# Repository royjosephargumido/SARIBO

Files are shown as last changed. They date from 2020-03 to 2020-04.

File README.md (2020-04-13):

# Overview
  
**SARIBO** or ***Systematic and Automated Regulation of Irrigation systems for Backyard farming Operations*** is an internet-of-things (IOT) Irrigation System designed for Backyard Farming created using ESP8266 NodeMCU 12E v3 (LoLin). SARIBO is a waray-waray (Waray) term for "to water" especially for plants.

SARIBO contains two modules:

1. **SARIBO Leaf Module (SARIBO Leaf).** The SARIBO Leaf Module which controls the connected sensors and is placed on the field.
2. **SARIBO Root Module (SARIBO Root).** The SARIBO Root Module is the main controller module which controls the watering process, activation of relays for the pump and valves, water level among others.

# Stable Version

See the official stable version @ **[Official Stable Release SARIBO version 1.2.7](https://github.com/rjargumido/SARIBO/releases/tag/v.1.2.7)** Source codes for the module are available at the "*Releases*" folder.

# Pin Configuration

**Leaf Pin Configuration:**

| **Label** | **Pin** | **Part** |
| --- | --- | --- |
| VCC | VCC/VIN | All with VCC/VIN 5VDC+ |
| GND | Gnd | Ground Pin |
| A0 | A0, Analog | Soil Moisture Sensor |
| SCL | D1/GPIO 5 | RTC Module |
| SDA | D2/GPIO 4, PWM | RTC Module |
| CS | D8/GPIO 15, PWM | SD Card |
| SCK | D5/GPIO 14, PWM | SD Card |
| MOSI | D7/GPIO 13 | SD Card |
| MISO | D6/GPIO 12, PWM | SD Card |

# Root Diagram

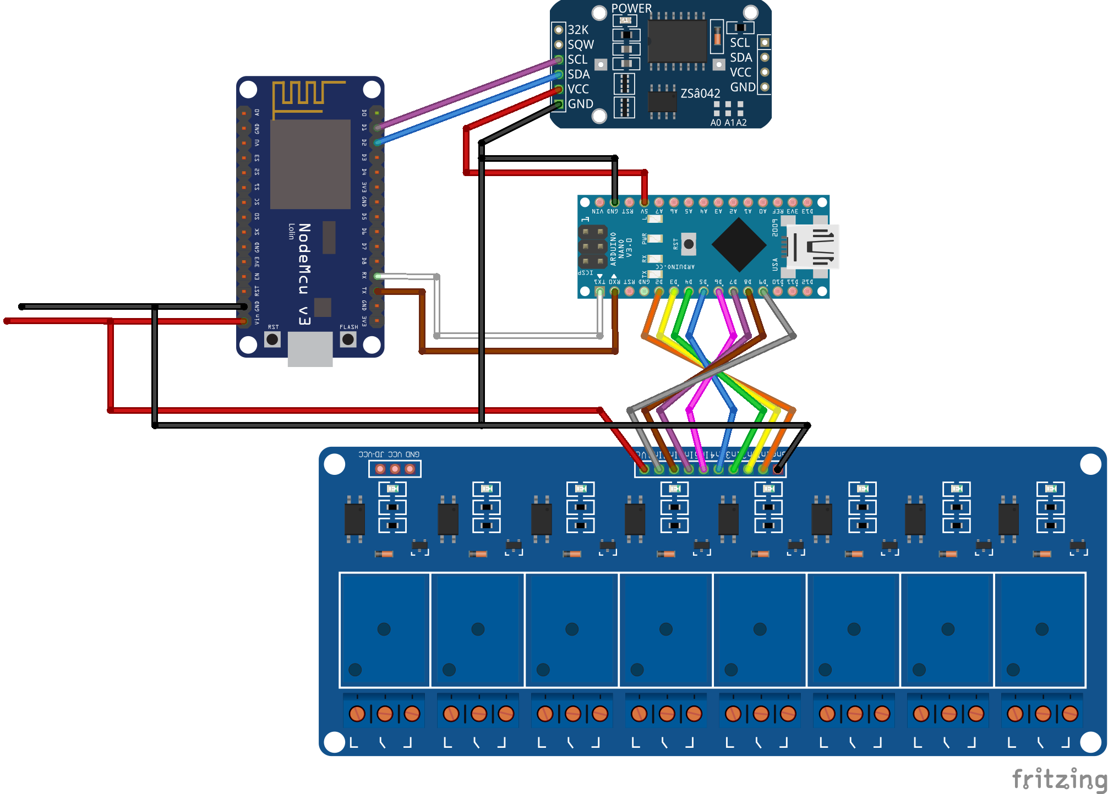
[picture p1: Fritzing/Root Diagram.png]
Root Fritzing Diagram


# Leaf Diagram

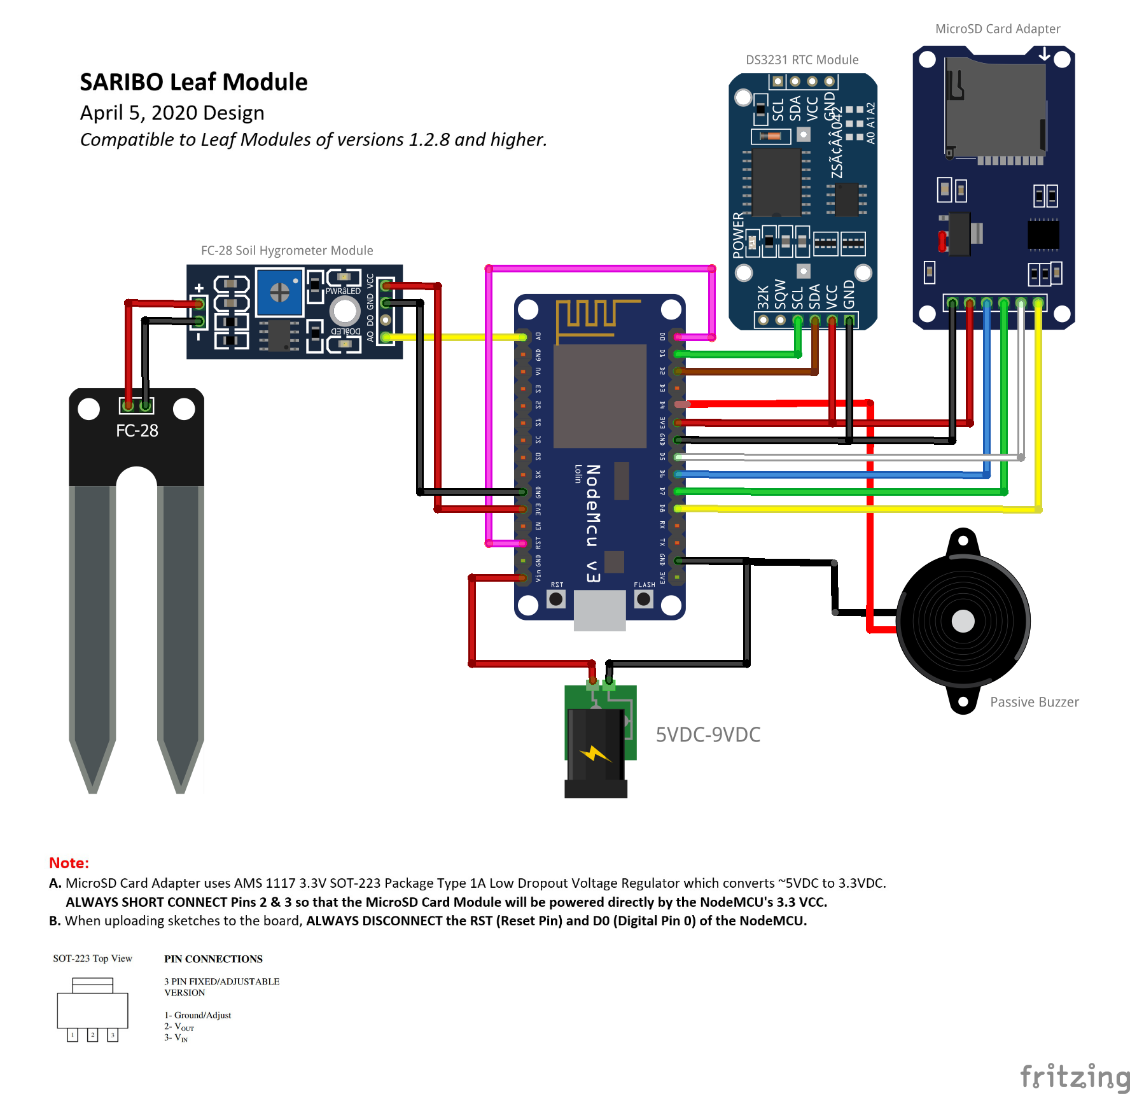
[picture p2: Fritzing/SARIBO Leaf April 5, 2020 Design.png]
SARIBO Leaf Diagram (April 5, 2020 Design)


# Hardware Requirements
The following are the hardware requirements for SARIBO:

| **Hardware** | **Description** |
| --- | --- |
| NodeMCU V3 ESP8266 ESP-12E (LoLin)  | Serves as the micro controller unit (MCU) that performs the functionality of the system. |
| 12V DC Plastic Solenoid Water Valve (Normally Closed) 1/2"| Used in opening individual Leaf Distribution Lines. |
| Plastic Water Flow Sensor 1/2" | Used to determine the water flow rate. |
| MicroSD Card Reader Module | Data logging functions. |
| 2, 4-Channel 5V Low Level Trigger 10A 250 VAC Relay with Optocoupler | Relays used in controlling the pump and other higher voltage devices. |
| DS3231 RTC Real Time Clock and EEPROM AT24C32 Module | Provides the date and time functionalities. |
| HC-SR04 Ultrasonic Ranging Sensor | Used in determining the water level in the tank/reservoir.  |
| Soil Moisture Sensor Module | Used in determining the soil moisture level. |
| 74HC595 Shift-Out Register | Additional output pins. |

# Software Requirements
The following are the software requirements for SARIBO:

| **Software** | **Specification** | **Description** |
| --- | --- | --- |
| Arduino IDE | Version 1.8.10 | Serves as the Integrated Development Environment (IDE) of the Arduino wherein codes during the development are written using the software. |
| ArduinoJSON Library for Arduino | Built using [<ArduinoJson.h> ArduinoJson Library version 6.14.1 by Benoit Blanchon](https://github.com/bblanchon/ArduinoJson). | An Arduino library used as the parser/decoder (serializer/deserializer) of data of the system that will be sent via the Wi-Fi communication of the modules of the system. |
| SD Library for Arduino | Built using [<SD.h> SD Library version 1.2.4 by Arduino.cc and SparkFun](https://www.arduino.cc/en/Reference/SD). | An Arduino library used for the data logging purposes. |
| SPI Library for Arduino | Built using [<SPI.h> Serial Peripheral Interface Library by Arduino](https://www.arduino.cc/en/Reference/SPI). | An Arduino library used for transferring data between microcontrollers and other small devices. |
| Real Time Clock (RTC) Library for Arduino | [<RTClib.h> Version 1.3.3 by AdaFruit](https://github.com/adafruit/RTClib) | Provides the functionality for the setting and accessing of date and time. |
| HCSR04 Ultrasonic Ranging Sensor Library for Arduino | Built using [<HCSR04.h> version 2.0.2 by gamegine](https://github.com/gamegine/HCSR04-ultrasonic-sensor-lib). | Provides the functionality for the control and use of the HCSR04 Ultrasonic Ranging Sensor Module used in determining the water level in the tank. |
| ESP8266 Board for Arduino | Version 2.6.3 by the ESP8266 Community [ESP8266 Libraries](https://github.com/esp8266/Arduino) and [ESP8266 Board](http://arduino.esp8266.com/stable/package_esp8266com_index.json). | Provides the Wi-Fi communication and Web Server functionality. |
| ESP8266 Wi-Fi Library for ESP8266 NodeMCU | <ESP8266WiFi.h> Based on WiFi.h from Arduino WiFi shield library. Copyright (c) 2011-2014 Arduino. Modified by Ivan Grokhotkov, December 2014. Provided in the esp8266 Arduino board. | This provides the functionality in configuring the network settings such as setting the network SSID, the SSID password, ports to be used, IP address, the subnet and other communication related settings. |
| ESP8266 Web Server Library for ESP8266 NodeMCU | <ESP8266WebServer.h> Copyright (c) 2014 Ivan Grokhotkov. Provided in the esp8266 Arduino board. | This provides the network router or the web server that serves as the address or the routes wherein date could be sent or retrieved. |

# Data Management Service
SARIBO does not implement any database management systems (DBMS) in managing its data. Data are managed through the use of [*ArduinoJson Library v6.14.1 by Benoit Blanchon*](https://arduinojson.org/v6/assistant/) and saving it in a plain text file (.txt).

Data Management Service is further divided into the following content flaggers:
1. **DMS-Meta-Data**
2. **DMS-FSS**
3. **DMS-Body**

**1. DMS-Meta-Data** The *DMS Meta-Data* contains the information about the file.

| **Data** | **Description** | **Sample Value** | **Data Type** |
| --- | --- | --- | --- |
| header | What data is stored in the file. | LEAF-SETTINGS | String |
| dmsversion | What DMS version is used. | 1.2.3 | String |
| dcreated | The date the file is created in local format. | April 1, 2020 | String |
| tcreated | The time the file is created in local format. | 16:05:32 | String |
| owner | Who created the file (user id). | ADMIN04072020160532 | String |
| dmodified | The date where the file is last modified. | April 1, 2020 | String |
| tmodified | The time where the file is last modified. | 16:22:47 | String |
| modifiedby | Who modified the file (user id). | ADMIN04072020162012 | String |
| umode | How the file is updated*. | SD-SIGNED | String |

**Update Mode:**
1. ***SD-SIGNED.*** Happens when the Leaf's MicroSD Card is inserted in to the Root's Leaf SD Setup Port.
2. ***NET-SIGNED*** Happens when the Leaf's Settings File (SysConfig.txt) is being updated automatically via the network during Leaf POST.

**2. DMS-FSS** The *DMS-FSS* or the Data Management Service - File Structuring Standard (as can be seen in the next chapter), are the file structuring scheme used in the current SARIBO device/version. DMS-FSS complies with the File Structuring Standard as can be seen in the next chapter.

| **Data** | **Description** | **Sample Value** | **Data Type** |
| --- | --- | --- | --- |
| device | SARIBO Module | LEAF | String |
| repdir | Replication directory name. | Replication | String |
| coredir | The Core Configuration Directory name. | System | String |
| logsdir | The POST Log directory name. | Logs | String |
| corefn | Core configuration file name. | CoreConfig.txt | String |

**3. DMS-Body** This contains all the data neccessary for the device (device @ DMS-FSS).

| **Data** | **Description** | **Sample Value** | **Data Type** |
| --- | --- | --- | --- |
| local | The Leaf's HID | 2J41F7FQ | String |
| root | The Root's HID | HSDOSSUR| String |
| ssid | SARIBO WiFi Access Point | SARIBO - NwSSU | String |
| key | WAP Password | 123456789 | String |
| host | Host IP Address | 192.168.4.1 | String |
| reqpath | URL Path | /requests/?data= | String |
| port | Port where requests is to be sent. | 80 | Integer |
| coredir | The core configuration directory. | 
| wut | The time when the Leaf module should wake up. | 6:00:00 | String
| maxdryness | Maximum soil dryness | 1001 | Integer |
| mindryness | Minimum soil dryness | 600 | Integer |
| idealmoist | Ideal soil moisture | 450 | Integer |

# File Structuring Standard
The SARIBO modules strictly follow file structuring schemes:

**Leaf File Structuring:**

    FileSystem:
    |
    +---Core
    |   |
    |   +--- "Source Codes for the Leaf Module"
    |
    +---Documentation
    |   |
    |   +--- SARIBO User Manual.pdf
    |
    +---Logs
    |   |
    |   +--- CSV
    |   |     |
    |   |     + --- "CSV-2J41F7FQ-00001.csv"
    |   |
    |   +--- POST
    |        |
    |        + --- "POST-2J41F7FQ-00001.txt"
    |
    +---Replication
    |   |
    |   +--- Logs
    |   |
    |   +--- Root
    |
    +---System
        |
        +--- CoreConfig.txt

**Root File Structuring:**

    FileSystem:
    |
    +---Core
    |    |
    |    +--- "Source Codes for the Leaf and Root Modules"
    |
    +---Documentation
    |    |
    |    +--- SARIBO User Manual.pdf
    |
    +---Leaf
    |    |
    |    +---"Leaf's Hardware Id"
    |        |
    |        +--- Configuration
    |        |
    |        +--- POST
    |
    +---Logs
    |    |
    |    +--- POST
    |
    +---System
         |
         +--- Resources
         |
         +---HID.txt
         |
         +---SysConfig.txt

**Note:**
1. ***HID.txt*** contains all Hardware Ids in the network. Database of Hardware Ids.
2. ***SysConfig.txt*** or the system configuration database contains all the settings of the Root module.

# Data Exchange Standard (DES)

The Data Exchange Standard (DES) is used as the core data exchange, transfer, response, and processing rules used to ensure that the data is being processed the same way throughout the system. It is further divided into five:

1. **Data Exchange Standard Guidelines** Is the set of rules and guidelines for the Data Exchange Standard.
2. **Exchange Table** Is the table used in exchanging requests and responses in the network.
3. **Requests Code** Are 2-digit integer code used for determining what type of request is being sent or data to be send.
4. **Request** Is the table used in a request.
5. **Response** Is a table used in response to a request.

**1. Data Exchange Standard Guidelines**

1. ***For every request, there should be a response.***
2. The Transaction Id has the format of: *leafHID-YYYYMMMDD-HHMMSS* e.g. HC7E9701-2020Apr1-70209
3. Hardware Ids should comply with the Hardware ID Management Service (HIMS).
4. The Date object is in the format: MMMM dd, YYYY e.g. April 1, 2020 without the zero padding in the day object.
5. The Time object is in the format: hh:mm:ss SS e.g. 7:02:09 AM with the zero padding on both minute and second objects only.
6. Request codes complies with the recent Request Code Table under the Data Exchange Standard.
7. For ****requests only***, all space characters ' ' should always be replaced with the plus character '+' for URI/URL compliance.

**2. Exchange Table**
The Exchange Table is the standard table used in exchanging requests and responses in the network.
Exchange Table v2.3 revision April 1, 2020

| **Data**  | **Description** | **Data Type** |
| --- | --- | --- |
| transid | the Transaction Id signed by the Requesting module | String |
| origin | The Hardware ID of the requesting module | String |
| destination | The Hardware ID of the destination module of the request | String |
| datesent | The current date of the requesting module | String |
| timesent | The current time of the requesting module | String |
| request | The request code | Integer |
| value | The value being exchange as a validation/required data | String |

**3. Requests Code**
The following are the request codes under Request Code Table v2.1 revision March 31, 2020:

| **Request Code**  | **Description** |
| --- | --- |
| 10 | General Leaf Distribution Line Response |
| 11 | Leaf Distribution Line, Open |
| 12 | Leaf Distribution Line, Close |
| 20 | Get Leaf Water Flow Rate Reading |
| 21 | Read current Leaf Water Flow Rate |
| 30 | Power Reading Only |
| 40 | Date and Time reading |
| 41 | Synchronize with Root Date and Time settings |
| 50 | Network Reading |
| 51 | Ping Request |
| 61 | Pull Root Settings |
| 62 | Pull Leaf Settings |
| 71 | Soil moisture reading only |
| 72 | Request for a Hardware ID |

**4. Request**
The following is a sample request:

| **Data** | **Content** |
| --- | --- |
| transid | HC7E9701-2020Apr1-70209 |
| origin | HC7E9701 |
| destination | RBF0928J |
| datesent | April 1, 2020 |
| timesent | 7:02:09 AM |
| request | 11 |
| value | 892 |

The above request generates a string value of:
*{"transid":"HC7E9701-2020Apr1-70209","origin":"HC7E9701","destination":"RBF0928J","datesent":"April+1,+2020","timesent":7:02:09+AM","request":11,"value":892"}*

**5. Response**
The following is a sample response to the above sample request:

| **Data** | **Content** |
| --- | --- |
| transid | HC7E9701-2020Apr1-70209 |
| origin | RBF0928J |
| destination | HC7E9701 |
| datesent | April 1, 2020 |
| timesent | 7:02:48 AM |
| request | 10 |
| value | Leaf01 Open Distribution Line request approved. |

The above request generates a string value of:
*{"transid":"HC7E9701-2020Apr1-70209","origin":"RBF0928J","destination":"HC7E9701","datesent":"April 1, 2020","timesent":7:02:48 AM","request":10,"value":"Leaf01 Open Distribution Line request approved."}*

# Hardware ID Management Service (HIMS)

The Hardware ID Management Service (HIMS) is the core function that process the naming of modules *(giving of hardware Id)*, and the decoding of HIDs present in the Data Exchange Table for the processing of requests.

**HIDs are 8 pseudo-random generated alphanumeric codes used to name modules for easier network data exchange.*** HIMS serves as the central registration authority of hardware Ids within a specific SARIBO network and ensures that generated HIDs only belongs to the network, and are uniquely generated.

**The Generate Hardware ID Algorithm**
The following is the algorithm used in generating HIDs:

1. To create a psuedo-random number, the randomSeed() in the setup() function is placed
2. Randomize between 0 & 1. If value is 1 store a psuedo-random uppercase alphabet character, otherwise a psuedo-random numeric character.
3. Repeat step #2 until 8 alphanumeric characters are generated.
4. Return the character array as a String

The source code for the generation of hardware id is here at [Generate Hardware Id](https://github.com/rjargumido/SARIBO/blob/master/Individual%20Systems/generateHardwareID/generateHardwareID.ino).

# Soil Moisture Reading Guidelines
The following is the algorithm employed in reading and processing of the soil moisture:

**1.** Read the soil moisture value once every second for one minute for accuracy and save it in a *long int* data type variable.

**2.** After 1 minute, compute the final soil moisture value and divide it by 60.

**3.** Load user soil moisture level configuration such as the *maxsoildryness*, *minsoildryness* and the *idealsoilmoist* values from SD card.

**4.** Perform additional processes based on the following:

   **a.** When the **final soil moisture is above the maximum soil dryness**, repeat reading of the soil moisture. ***Go to step 1***;
   **b.** When the **final soil moisture is between the maximum soil dryness and the minimum soil dryness** (*means that the soil is dry*), trigger the **OPEN distribution request**, ***Go to step 5***;
   **c.** When the **final soil moisture is between the minimum soil dryness and the ideal soil moisture** (*means that the soil is in the ideal soil moisture*),:
          **c.1.** Check if there is already a sent open distribution line request, if true, ***Go to step 6***, else, trigger the **Soil Moisture Reporting Only**;

**5.** After 4 minutes from the *OPEN distribution request*, ***repeat steps 1-4***;

**6.** Send **CLOSE distribution request**;

***Note:*** Always create a high verbosity log.

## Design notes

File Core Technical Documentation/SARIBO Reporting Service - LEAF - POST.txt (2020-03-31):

SARIBO REPORTING SERVICE
Version 2.2, Revision March 17, 2020
**************************************************
Power On Self Test Log
/logs/POST/POST_Mar-1-2020.txt

SARIBO L1

March 1, 2020
6:58:56
**************************************************
Starting Power On Self Test...

6:58:58

Checking network configurations...
Server SSID: Hydra Server - NwSSU
Server IP Address: 192.168.11.4
Port: 80
Pinging 192.168.11.4...
Leaf01: Ping request sent to server on 1 March, 2020 7:00:1
Server: Server responded at 204 ms.
Ping ok. Server available.

7:00:10

Synchronizing date and time with Server...
Leaf01: DateTime request sent to server on 1 March, 2020 7:01:4
Server Date: March 1, 2020
Server Time: 7:01:28
Local Date: March 1, 2020
Local Time: 7:01:28
Date and time synchronized.

7:01:30

Checking power status...
Voltage: 3.37
Capacity: 58%
Leaf01: Power status report sent to server on 1 March, 2020 7:01:52
Server: Leaf01 power status recorded.
Power status ok.

7:02:14

Performing soil moisture check...
Activating soil moisture sensor...
Soil moisture sensor activated.
Performing soil moisture reading...
***
Soil Moisture Reading #1: 478
Soil Moisture Reading #2: 477
Soil Moisture Reading #3: 478
...
Soil Moisture Reading #58: 468
Soil Moisture Reading #59: 470
Soil Moisture Reading #60: 474
***
Average soil moisture: 474
Soil is in ideal soil moisture level.
Leaf01: Soil moisture report sent to server on 1 March, 2020 7:03:17
Server: Leaf01 soil moisture status recorded.
Soil moisture reading ok.

7:03:17

Performing watering...
Running watering confirmation check...
Leaf01: Watering request sent to server on 1 March, 2020 7:03:22
Server: Leaf01 open distribution request approved. Opening valve in 5 seconds.
Performing water flow rate reading...
***
Water flow Reading #1: 1.77 ml./sec.
Water flow Reading #2: 1.77 ml./sec.
Water flow Reading #3: 1.77 ml./sec.
Water flow Reading #4: 1.77 ml./sec.
Water flow Reading #5: 1.75 ml./sec.
***
Average water flow rate: 1.76 ml./sec.
Water verified at the last sprinkler.
Leaf01: Watering report sent to server on 1 March, 2020 7:04:12
Server: Leaf01 watering report recorded. Leaf01 distribution valve closed.
Leaf01 water valve ok.
Water flow reading ok.
Water sensor ok.

7:05:28
Network configuration: Good
Server: Available
DateTime: Synchronized
Power: 58%
Average soil moisture: 474
Soil Moisture reading: Ok
Distribution valve: Ok
Average water flow rate: 1.76 ml./sec.
Water flow reading: OK

Network: Active
Server Reporting Service: Active

End of Power On Self Test reporting.
**************************************************
Leaf01: POST log sent to server. 1 March, 2020 7:06:7
Server: Leaf01 POST log successfully recorded. Signed SARIBO ROOT - NwSSU @ 192.168.11.4 on March 1, 2020 7:06:36

{803C8A5D-CA6B-41EA-B572-76C9C86AA322}

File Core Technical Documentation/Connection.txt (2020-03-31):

NRF240L

CE	YELLOW	D8
SCK	GREEN	D13
MISO	PURPLE	D12
CSN	ORANGE	D8
MOSI	BLUE	D11

ROOT NANO

A0	
A1
A2
A3
A4	RTC	SDA
A5	RTC	SCL
A6
A7

D2	RELAY 1
D3	SD	CS
D4	RELAY 2
D5	SR	RCLK
D6	SR	SRCLK
D7	RELAY 3
D8	RELAY 4
D9	US	TRIG
D10	US	ECHO
D11	SD	MOSI
D12	SD	MISO
D13	SD	SCK

ROOT NODEMCU

D1	Relay 1	Pump
D5	Relay 2	Main Valve
D6	Relay 3 Refill Valve
D8	Relay 4 Discharge Valve

LEAF

A0	SM	A0	Soil Moisture
A1
A2
A3
A4	RTC	SDA	Real time Clock
A5	RTC	SCL	Real time Clock
A6
A7

D2	WF		Water Flow sensor
D3	SD	CS	SD Card module
D4
D5
D6
D7
D8	
D9
D10
D11	SD	MOSI	SD Card module
D12	SD	MISO	SD Card module
D13	SD	SCK	SD Card module

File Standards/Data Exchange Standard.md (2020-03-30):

# Data Exchange Standard (DES)

The Data Exchange Standard (DES) is used as the core data exchange, transfer and processing rules used to ensure that the data is being processed the same way throughout the system. It is further divided into two:

1. **Data Exchange Table** Is a table that is being used to consolidate relevant real-time data to be used in the exchange between the Leaf and the Root modules or vice versa.
2. **Requests** Are 2-digit integer code used for determining what type of request is being sent or data to be send.

# Requests

The following are the request codes under Request Code Table v2.1 revision March 31, 2020:

| Request Code  | Description |
| --- | --- |
| 10 | Soil moisture reading only |
| 11 | Leaf Distribution Line, Open |
| 12 | Leaf Distribution Line, Close |
| 20 | Get Leaf Water Flow Rate Reading |
| 21 | Read current Leaf Water Flow Rate |
| 30 | Power Reading Only |
| 40 | Date and Time reading |
| 41 | Synchronize with Root Date and Time settings |
| 50 | Network Reading |
| 51 | Ping Request |
| 61 | Pull Root Settings |
| 62 | Pull Leaf Settings |

# Data Exchange Table
The following is the table structure used under Data Exchange Table v2.2 revision March 31, 2020:

| Data  | Description |
| --- | --- |
| origin* | The Hardware ID of the requesting module |
| destination* | The Hardware ID of the destination module of the request |
| datesent** | The current date of the requesting module |
| timesent*** | The current time of the requesting module |
| request****  | The request code |
| value  | The value being exchange as a validation/required data |

Note:
* Complies with the Hardware Id nomenclature Algorithm found at the Root Hardware ID Management Service (HIMS).
** The Date object is in the format: MMMM dd, YYYY e.g. April 1, 2020 without the zero padding in the day object.
*** The Time object is in the format: hh:mm:ss SS e.g. 7:02:09 AM with the zero padding on both minute and second objects only.
**** Request codes complies with the recent Request Code Table under the Data Exchange Standard.

Example:

origin : HC7E9701
destination : RBF0928J
datesent : April 1, 2020
timesent : 7:02:09 AM
request : 11
value : 892

The above Data Exchange Table returns a string value of:
*{"origin":"HC7E9701","destination":"RBF0928J","datesent":"April+1,+2020","timesent":7:02:09+AM","request":11,"value":892"}*

The following followwing String value complies with the ArduinoJson object [*see: <ArduinoJson.h> ArduinoJson Library version 6.14.1 by Benoit Blanchon*](https://arduinojson.org/v6/assistant/) and the HTTP URL/URI standards.

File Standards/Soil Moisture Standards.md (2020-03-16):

Soil Moisture, and Reading Standards v. 1.0 rev Mar. 16, 2020
-----------------------------------------------------------

Pin configuration
-----------------------------------------------------------
The Soil Moisture sensor (MHI sensor series) uses the following connection to Arduino

| Soil Moisture  | Arduino Pin |
| --- | --- |
| VCC+ | 5V VCC+ |
| GND | Gnd |
| A0 | A0 |

Soil Moisture Reading Algorithm
-----------------------------------------------------------
**1.** Read the soil moisture value (AnalogRead(pin)) once every second (60 counts) for one minute for accuracy and save it in a *long int* data type.

**2.** After 60 counts, compute the final soil moisture value and divide it by 60.

**3.** Load user soil moisture level configuration such as the *maxsoildryness*, and the *minsoildryness* from SD card (/core/SYSCONFIG.txt)

**4.** When the final soil moisture is between the *maxsoildryness* and the *minsoildryness* range (means the soil is dry), trigger the *OPEN distribution request*, ***go to line 5***, else, trigger the *CLOSE distribution request*.

**5.** After 4 minutes from the *OPEN distribution request*, ***repeat steps 1-4***

***Note:*** Always create a high verbosity log.

Source Code
-----------------------------------------------------------
```arduino

int count = 1;              // Used in calculating the number of soil moisture check
bool stopCheck = false;     // Used as a counter whether to continue or stop the soil moisture reading
unsigned long oldTime;      // Used in calculating the  seconds passed since the initial time reading 
long int soilmoisture = 0;  // The soil moisture value is saved as a long data type to cater higher precission

void checkSoilMoisture()
{
  int finalSoilMoisture = 0;
  
  if(stopCheck == false)
  {
    /* 
     * reads and compute the average soil moisture sensor
     * once every second for 1 minute for better accuracy
     */
    if(((millis() - oldTime) > 1000) && count < 61)
    {
      soilmoisture += analogRead(A0);   // Reads the soil moisture and adds the old readings

      /*
       * Displays the data for verification
       */
      Serial.print("Reading #");
      Serial.println(count);
      Serial.print("Soil moisture: ");
      Serial.println(soilmoisture);
    
      oldTime = millis();   // Saves the the number of milli seconds past since the reading
      count = count + 1;    // Used in the reading for 1 minute
    }

    // Stops soil moisture reading until 1 minute (60 seconds)
    if(count == 60)
    {
      oldTime = 0;       // Resets the millisecond timer
      count = 0;        // Resets the number of seconds counter
      stopCheck = true; // Stops the reading of the soil moisture
      finalSoilMoisture = soilmoisture / 10;  // Calculates the average soil moisture value
      
      Serial.print("Final Soil moisture: ");
      Serial.println(finalSoilMoisture);

      //load the configurations from /System/SYSDEF.TXT
      int maxsoildryness = 1001;    //Maximum soil dryness value
      int minsoildryness = 500;     //Minimum soil dryness value

      if(finalSoilMoisture < maxsoildryness && finalSoilMoisture > minsoildryness)
      {
        /* 
         * Soil is DRY based from the range of the Soil Dryness set by the user
         * then creates an open distribution valve request to the Root module
         * sending the final soil moisture value as a validating value for double checking.
         * 
         * 101 = code for OPEN distribution valve request as specified in the data request table
         */
        createRequestTable(11, finalSoilMoisture);
        Serial.print("Open Leaf01 distribution valve request sent.");
      }
      else if(finalSoilMoisture < minsoildryness)
      {
        /* 
         * Soil is WET when the final soil moisture value is lesser than the
         * minimum soil dryness threshold value then creates a close distribution 
         * valve request to the Root module and attaches the final soil moisture
         * value as a validating value for double checking.
         * 
         * 102 = code for CLOSE distribution valve request as specified in the data request table
         */
        createRequestTable(12, finalSoilMoisture);
        Serial.print("\n\nClose Leaf01 distribution valve request sent.");
      }
    }
  }
}
```

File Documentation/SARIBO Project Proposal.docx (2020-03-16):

S.A.R.I.B.O.

(Systematic and Automated Regulation of Irrigation systems for

Backyard farming Operations)

An Arduino-based Internet-of-Things Irrigation System designed for Backyard Farming

Submitted to:

JEFFREY C. NIEDO

ITE-6 Instructor

Submitted by:

Rica S. Bohol

Jemaima D. Depanzo

Roy Joseph B. Argumido

March 3, 2020

Overview

The advancement of technology today is inevitably and regularly updating. New technologies such as home and farm automation that uses wireless connections prove that every day, innovation is possible. The management and processes of people specifically farmers and gardener’s day to day life, like monitoring and managing of gardens or farms can be improved through the use of innovation and of the present technologies.

Technology is indeed becoming more advanced as the day passes, and the proponents established the idea that the processes performed in gardens and farms can be automated. Existing garden and farm processes heavily rely in traditional methods which is requiring too much effort and time. This includes processes such as fetching water, storing and refilling of water to the water tank, watering the plants, and farmers, and even gardeners needs to constantly go to their farms or gardens to check for the dryness of the soil. These issues are the main reasons why the researchers conducted this study.

Through this study, the proponents will develop and implement an automation system to eliminate or reduce the time and effort exercised to carry out these processes. This will address the issue of fetching, and storing of water, refilling of water tank, and watering the plants. Through this study, a water tank is used wherein the refill, drain and checking the water level in the tank uses electrical devices that reduces and eliminates the amount of work done and checking the level of soil moisture could be processed in real time without the user to go to the farm or garden. This will employ sensors and microcontroller unit that gathers and processes data from the field, the use of higher voltage devices such as relays for the control of pump and valves, and other devices and sensors that gathers, store and send data such as SD Card modules among others.

The system will be named “SARIBO”, a waray-waray term for “to water” such as to water plants. SARIBO stands for Systematic and Automated Regulation of Irrigation systems for Backyard farming Operations, is an IOT (internet-of-things) enabled project using Arduino and NodeMCU ESP8266 that is designed for the automation of irrigation processes of backyard farming. SARIBO has two separate modules – the Root module which controls the main controller functionalities such as tank refill, drain and distribution, opening of valves for specific plots (distribution lines), the overall management of the Wi-Fi network, central data repository, SMS notification, date and time functionalities, among other major system functions, and the Leaf module that manages the processes present in the plots (distribution lines) such as checking the soil moisture level, sending data request to the Root module, and other functionalities.

The proponents believe that the system that will be developed and implemented will solve the stated problems. Through the use of the system, its users

would have convenience in monitoring and controlling electrical power switch at

home.

Organizational Description

Background

There is a quote that is very accurate in describing a farmer, according to Wendel Berry “Farmers farm for the love of farming. They love to watch and nurture the growth of plants. They love to live in the presence of animals. They love to work outdoors. They love the weather, maybe even when it is making them miserable”. Every farmers mind set is to produce a healthy crops or animals in order to feed people for a living. They are so much into taking care of their plants and producing the best of it not just in order to give themselves food for living but also to gain money to survive in this world, no matter how bad or good the weather is all of the farmers instinct is to have a great harvest.

Mission

To collectively empower farmers and fisher folk and the private sector to increase agricultural productivity and profitability, taking into account sustainability and resilience.

Vision

A food secure Philippines with prosperous farmers and fisher folk.

Business Process

Problem Statement

According to the House Bill No. 1718, agriculture is the traditional backbone of Philippine economy and the principal source of employment, employing almost half of the total labor force. It has been considered as a major industry source of the Philippines due to the fact that we are an agricultural country which in fact, our country relies heavily in agriculture. However, farmers were observed to use the traditional way of farming instead of adapting new agricultural technologies, which made the agribusiness farms productive and profitable.

Farmers can use the inventions of agricultural technology in order for it to maintain the growth of its crops and even in maintaining the supply of the water whenever there are weather interruptions or any other occurrence might come along.

After identifying the problems, opportunities, objectives, and constraints throughout the making of the study, a matrix has been made.

Objective

The proponents aim to develop and implement an Internet-of-Things (IOT) Automated Plant Watering System for farmers, gardeners, hobbyists, plant collectors, or even individuals who owned a backyard farm or garden and have the following objectives:

a. eliminate or reduce the throughput or the amount of work being performed in fetching water;
b. eliminate or reduce the throughput or the amount of work being performed in storing water;
c. eliminate or reduce the throughput or the amount of work being performed in watering the plants; and to
d. eliminate or reduce the throughput or the amount of work being performed in measuring or detecting the dryness of the soil.

Scope and Limitation

The system is designed for the development of A Proposed Internet-of-Things (IOT) Automated Plant Watering System for farmers, gardeners, hobbyists, plant collectors, or individuals who owned a backyard farm. The following queries are the scopes and the limitations of the proposed system are as follows:

Scope:

1. Able to detect soil moisture.

The system is capable of detecting the moisture of the soil, it is the way of monitoring used whether the plants need to be watered or not.

2. Fully automated plant watering.

The system is designed to automatically water the plants in terms of the moisture of the soil, and if it's detected that the plant is in need of watering then the system leaf will be communicated to the root and request for a water.

3. Fully automated water tank refill.

The system well automatically refill tank before distributing water to the leaf or the system will distribute water first and then refill, It is the two sittings which is: Refill first before discharge and discharge first then refill.

4. Provides detailed and accurate system activity logs.

The system will automatically record everything that the system does.

5. Equipped with a SMS notification.

The system is designed with an SMS notification. It is capable of notifying the user whether an interruption occurred on the functionality of the systems either a malfunction happened or any other occurrence.

6. Running on Wi-Fi with a range of 250 meters.

The system is applicable on the field ranging about 250 meters.

7. Fully customizable settings.

The system is designed depending on what the users wants to from the overall setting of the system. Also, its either time based or according to the moisture of the soil. Then the setup of the apparatus depends also on the user when being implemented on the field.

8. Deep sleep mode functionality.

The Leaf is capable of hibernating, whenever it is night time or whenever there is no need to water plants the systems leaf will automatically hibernate itself.

Limitations:

1. Electrically powered main controller.

The main controller stops or it will not function whenever the electrical power is not available because the main controller is dependent to the electricity.

2. Poor-to-No network coverage in the area.

The SMS notification cannot be able to notify the user if there were no network connections.

3. Provides detailed and accurate system activity logs.

The system will automatically record everything that the system does.

4. Equipped with a SMS notification.

The system is designed with an SMS notification. It is capable of notifying the user whether an interruption occurred on the functionality of the systems either a malfunction happened or any other occurrence.

5. Running on Wi-Fi with a range of 250 meters.

The system is applicable on the field ranging about 250 meters.

6. Fully customizable settings.

The system is designed depending on what the users wants to from the overall setting of the system. Also, its either time based or according to the moisture of the soil. Then the setup of the apparatus depends also on the user when being implemented on the field.

7. Deep sleep mode functionality.

The Leaf is capable of hibernating, whenever it is night time or whenever there is no need to water plants the systems leaf will automatically hibernate itself.

REQUIREMENTS

Business Requirements Overview

Farmers, gardeners, hobbyists, plant collectors, or individuals who owned a backyard farm have been using the traditional way of farming. The traditional way of farming is considered to be exhausting in a sense that farmer need to take care of their plants in all way possible. It should be monitored by the farmers itself. And they had to be there in the process of growing, in terms of fetching water in order to water the plants, especially during dry seasons. So, because of that the farmers would not be able to do any other tasks they need to do in a daily basis it is because of the fact that they had to focus on checking out with there plants. Farming well take the time they can spent to other things and it would take their strength as well, and efforts well be exerted only on one task specifically monitoring there farm each day.

After knowing all those weary tasks of farming, the researchers come to a realization of proposing an Internet-of-Things (IOT) Automated Plant Watering System in response to the hardship of the farmers. This has been proposed in order to give ease in every farmers life.

Functional Requirement Specification of S.A.R.I.B.O. (Systematic and Automated Regulation of Irrigation systems for Backyard farming Operations):

Functionalities | Description
Work Breakdown Structure
Prototypes
Models and Diagram

Non-Functional Requirement Specification of the S.A.R.I.B.O. (Systematic and Automated Regulation of Irrigation systems for Backyard farming Operations):

Non-Functionalities | Description
Security
Capacity
Performance
Reliability
Timely
Availability

SYSTEM REQUIREMENTS

Hardware Requirements Specification of S.A.R.I.B.O. (Systematic and Automated Regulation of Irrigation systems for Backyard farming Operations):

Hardware | Specification | Description
Microcontroller Unit | Arduino Nano ATmega328P CH340G | The micro controller unit (MCU) responsible in the processing, management, control of the overall functionality of the system.
Wi-Fi Microcontroller Unit | NodeMCU V3 ESP8266 ESP-12E | The micro controller unit (MCU) responsible in the establishment, control, management, of the Wi-Fi communication functionality of the system.
Computer Set | ASUSTeK X540UP Intel(R) Core(TM) i7-7500U CPU @ 2.70GHz (4 CPUs), ~2.9GHz 4096MB RAM 64-bit operating system | The computer system used during the design and development of the system.
Water Valve | 12Volts DC Plastic Solenoid Water Valve (Normally Closed) ½” | The type of water valve used in controlling the water flow.
Water Flow Sensor | Plastic Water Flow Sensor ½” | The water flow sensor used in determining the rate of water flow in the pipes.
MicroSD Card Module | MicroSD Card Adapter for Arduino | Used for data logging functionalities.
Real Time Clock | DS3231 RTC Real Time Clock and EEPROM AT24C32 Module | Used for date and time functionalities.
Ultrasonic Ranging Sensor | HC-SR04 Ultrasonic Ranging Sensor | Used in determining the water level in the tank/reservoir.
Soil Moisture Sensor | Soil Moisture Sensor Module for Arduino | Used in determining the soil moisture level.
Custom made Pump | 12V/24V DC 775 Motor Double Ball Bearing | The custom pump used the 775 Motor.
Drip Irrigation Pipes | Drip/Atomizer Irrigation System Pipes | Pipes used in controlling the water output that is being supplied to the plants.
Distribution Pipes | ½” Blue PVC Pipe | Pipes used in the pump and distribution lines.
Relay | 4-Channel 5V Low Level Trigger 10A 250 VAC Relay with Optocoupler JQF-3FF-S-Z | Relays used in controlling the pump and other higher voltage devices.
DC to DC Converter | DC to DC Voltage Regulator Step Down Buck Converter Power Supply Module 9V/12V/24V/36V DC to 5V DC | Converts the 12V DC power that is supplied to the pump and other higher voltage devices to 5V DC which powers the microcontroller units and other sensors.
Power Supply | 12 Volts DC 3amp Power supply charger | Provides the power for the system.

Software Requirements Specification of S.A.R.I.B.O. (Systematic and Automated Regulation of Irrigation systems for Backyard farming Operations):

Software | Specification | Description
Operating System | Windows 10 Home Single Language 64-bit (10.0, Build 18362) (18362.19h1_release.190318-1202) | The operating system used during the development and design.
Integrated Development Environment (IDE) | Arduino IDE Version 1.8.10 | The Integrated Development Environment (IDE) of the Arduino wherein codes during the development are written.
CH340G Device Driver | Arduino Nano ATmega328P CH340G Device Driver | Enables the ability for the Arduino Nano to communicate with the computer's operating system and the Arduino IDE.
ESP8266 Board Device Driver | NodeMCU 12E version 3.0 ESP8266 Board Device Driver for Arduino | Enables the ability for the NodeMCU ESP8266 Board to communicate with the computer's operating system and the Arduino IDE.
ArduinoJSON Library for Arduino | ArduinoJSON Library Version 6.14.1 by Benoit Blanchon | An Arduino library used as the parser/decoder of data of the system that will be sent via the Wi-Fi communication of the modules of the system.
SD Library for Arduino | SD Card Library Version 1.2.4 by Arduino.cc and SparkFun | An Arduino library used for the data logging purposes.
Software Serial Communication Library for Arduino | Software Serial Communication Library for Arduino (SoftwareSerial.h) that is included in the Arduino Core libraries | Provides the functionality for the software serial communication between the Arduino Nano and the ESP8288 NodeMCU Wi-Fi Module.
Real Time Clock Library for Arduino | Real Time Clock Library for Arduino (RTClib.h) Version 1.3.3 by AdaFruit | Provides the functionality for the setting and accessing of date and time.
HCSR04 Ultrasonic Ranging Sensor Library for Arduino | HCSR04 Ultrasonic Ranging Sensor Library for Arduino (HCSR04.h) Version 2.0.2 by gamegine | Provides the functionality for the control and use of the HCSR04 Ultrasonic Ranging Sensor Module used in determining the water level in the tank.
Wi-Fi Library for ESP8266 NodeMCU | ESP8266 NodeMCU Wi-Fi Library (ESP8266WiFi.h) Copyright (c) 2011-2014 Arduino. Modified by Ivan Grokhotkov, December 2014 Provided in the esp8266 NodeMCU board. | This provides the functionality in configuring the network settings such as setting the network SSID, the SSID password, ports to be used, IP address, the subnet and other communication related settings.
Web Server Library for ESP8266 NodeMCU | ESP8266 NodeMCU Web Server Library (ESP8266WebServer.h) Copyright (c) 2014 Ivan Grokhotkov Provided in the esp8266 NodeMCU board. | This provides the network router or the web server that serves as the address or the routes wherein date could be sent or retrieved.

Human-Resource Requirements of S.A.R.I.B.O. (Systematic and Automated Regulation of Irrigation systems for Backyard farming Operations):

Peopleware | Role
Users | The users serve as the beneficiary of the system. They will be the end users who will be using the system.
System’s Analyst | The person in charge in the assessment and suitability of the intended outcomes or the objectives of the system and the communication with the end users. Systems analysts also serve as a researcher and agent who identify the organizational improvements needed, design systems to implement those changes, and train and motivate others to use the systems. The System Analyst together with the System Database Designer prepares the system documentation.
System’s Programmer | The person who writes program code logic and translate requirements into program. The System’s Programmer has duties that include the managing of the system’s performance, providing technical support, reviewing and updating existing programs and the modification of source codes, and identifying and fixing defects in the system. In this system, the System’s Programmer also serve as the Project manager and in addition to his tasks, he also manages the project and the team and give specific task to its project members.
System’s Database Designer | The person who is responsible for defining the detailed database design, system documentations and together with the System’s Analyst serve as a researcher and agent who identify the organizational improvements needed, design systems to implement those changes, and train and motivate others to use the systems.

Budgetary Requirements of S.A.R.I.B.O. (Systematic and Automated Regulation of Irrigation systems for Backyard farming Operations):

Item | Amount
Arduino Nano ATmega328P CH340G Soldered (2 pieces) | Php. 450.00 – (Php. 225.00 per piece)
NodeMCU V3 ESP8266 ESP-12E (2 pieces) | Php. 320.00 – (Php. 160.00 per piece)
12VDC Plastic Solenoid Water Valve (Normally Closed) 1/2" (5 pieces) | Php. 1,495.00 – (Php. 299.00 per piece)
MicroSD Card Reader Module (2 pieces) | Php. 158.00 – (Php. 79.00 per piece)
DC to DC Voltage Regulator Step Down Buck Converter Power Supply Module 9V/12V/24V/36V DC to 5V DC (1 piece) | Php. 70.00
4-Channel 5V Low Level Trigger 10A 250 VAC Relay with Optocoupler (2 pieces) | Php. 310.00 – (Php. 155.00 per piece)
Stepper Motor Coupler 5 mm. x 5 mm. (1 piece) | Php. 65.00
Plastic Water Flow Sensor 1/2" (3 pieces) | Php. 741.00 – (Php. 247.00 per piece)
DS3231 RTC Real Time Clock and EEPROM AT24C32 Module (2 pieces) | Php. 250.00 – (Php. 125.00 per piece)
HC-SR04 Ultrasonic Ranging Sensor (2 pieces) | Php. 174.00 – (Php. 87.00 per piece)
12V/24V DC 775 Motor Double Ball Bearing | Php. 499.00
Soil Moisture Sensor Module (2 pieces) | Php. 110.00 – (Php. 55.00 per piece)
¾” x 1 ½” PVC Pipe Reducer (Blue) (1 piece) | Php. 31.75
1 ½” PVC End Cap (Blue) (1 piece) | Php. 30.00
¾” PVC Pipe (Blue) (1 piece) | Php. 110.00
1 ½” PVC Pipe (Blue) (1 piece) | Php. 280.00
¾” PVC Elbow Pipe (Blue) (2 pieces) | Php. 34.00 – (Php. 17.00 per piece)
¾” PVC Tee Pipe (Blue) (4 pieces) | Php. 96.00 – (Php. 24.00 per piece)
Machine Screw with Nut 3/16 (2 pieces) | Php. 7.50 – (Php. 3.75 per piece)
Contact Cement Glue (1 piece) | Php. 39.00
Metal Epoxy (1 piece) | Php. 69.00
Drip Irrigation System (1 piece) | Php. 999.00
12V 3amp Power Supply (1 piece) | Php. 490.00
¾” Teflon Tape | Php. 10.00
Power bank Module (1 piece) | Php. 300.00
Passive Buzzer Module for Arduino AVR PIC (2 pieces) | Php. 70.00 – (Php. 35.00 per piece)
SIM800L V2 5V Wireless GSM GPRS Module (1 piece) | Php. 450.00
20x4 LCD Display Black on Green (1 piece) | Php. 200.00

Design Models (FDD, Context DFD, Level 0 DFD, Level 1 DFD (so on if possible), ERD)

Update User

Add user

Notification

Data Logger

Time Management

Relay

Water flow Rate

Network Reading

Data Logger

Network

Time Management

Power Management

Water flow Rate

Soil Moisture Checking

fill

efill

Tank Refill

Drain

Overflow

Tank Refill

fill

efill

Tank Refill

Distribution Discharge

Hydra: Automated Plant Watering System

Root Management

Leaf Management

Tank Management

Account Management

Schedule of Activities (Work Plan-Gantt Chart)

Activities | Weeks | | | | | | | | | | | | | | | Expected Output
| 1 | 2 | 3 | 4 | 5 | 6 | 7 | 8 | 9 | 10 | 11 | 12 | 13 | 14 | 15
Planning
Analysis
Design
Development
Testing

ISO 9001:2015 Certified Republic of the Philippines Northwest Samar State University Website: http//www.nwssu.edu.ph

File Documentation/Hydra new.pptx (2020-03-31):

## Hydra

Automated Plant Watering System

## What is Hydra?

Is a microcontroller-based automatic plant watering system.

## Hydra Modules

Hydra Root Module and the Hydra Leaf Module

## Hydra Root Module

The Hydra Root Module controls the overall management of the Hydra Network including all connected Hydra Leaf Nodes.

## Hydra Leaf Module

The Hydra Leaf Module controls the specific branch. It is responsible in checking the soil moisture and request to the Hydra Root for a water distribution.

## Features

## Hydra Features

- Automated watering based on user preferences such as time-based watering or when the soil is dry.
- Upgradable up to 16 independent on-field watering modules.
- Automatically detect the water level in the tank and initiates a refill process.
- Hydra Leaf is battery-powered that could run approximately 14 days to 31 days based on battery capacity.
- Data logging feature.
- Able to compute water consumption from different connected Hydra Leaf and adjusts automatically based on its consumption.
- Sends a text message to the user of system activities based on user preferences.

## Water Distribution Setup

Water Distribution Setup is based on the pump configuration either discharge only, no pump attached, discharge-refill configuration or either of the three.

## Legend

Water Valve

Water Flow Sensor

Water Drip/ Atomizer

Hose/ Water Line

Water Flow Direction

Optional Water Line

## Discharge Only

Pump

Tank

Drain

Field Lines

Branch Line

Distribution Line

Source
Line

Drain
Line

Source

- Tank-based
- Stable Main Water Source Pressure
- Pump is configured for water discharge purposes only
- Drain is optional
- Best suited for having a stable main water source water pressure esp. those with connections from the water district.

## Direct Distribution

Field Lines

Branch Line

Distribution Line

Source

Source
Line

- Unstable Main Water Source Pressure
- Pump is configured for water discharge purposes only
- Applicable only to main water source such as well.

Pump

## Discharge-Refill

Field Lines

Branch Line

Distribution Line

Discharge
Line

Source
Line

Source

Pump

- Tank-based
- Able to switch from direct source distribution, tank refill and tank-based water discharge.
- Drain is optional.
- Suitable for either stable and unstable water source pressure.

Tank

Discharge
Line

Drain
Line

Drain

## Components

## Soil Moisture Sensor

Features:
- Digital and analog output
- Working voltage: 3.3V-5V On-board LM393 chip
- Dimension: 3.2cm * 1.4cm
- Price: Php. 55

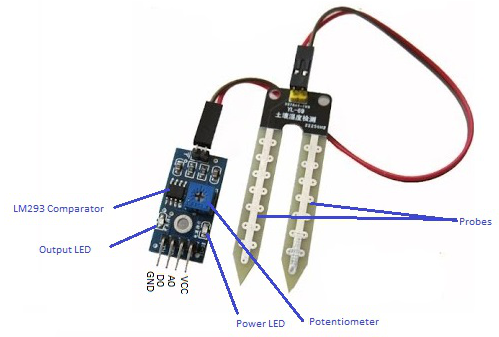
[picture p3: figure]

## Plastic Water Solenoid Valve

Features:
- ½ inch diameter PVC pipe
- 12V powered
- Minimum pressure requirement of 0.02 Mpa (3 PSI)
- Price: Php. 250

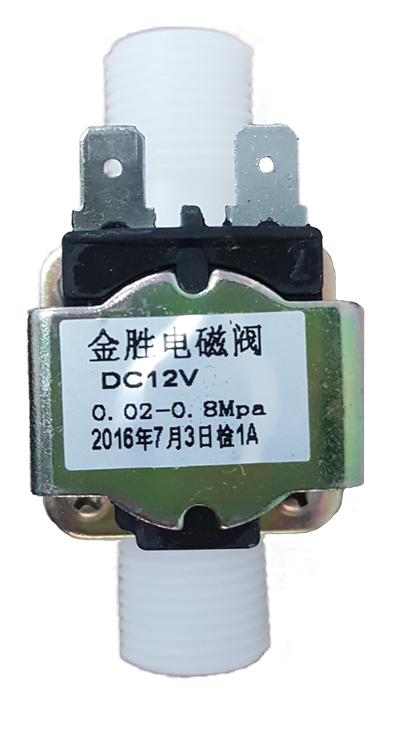
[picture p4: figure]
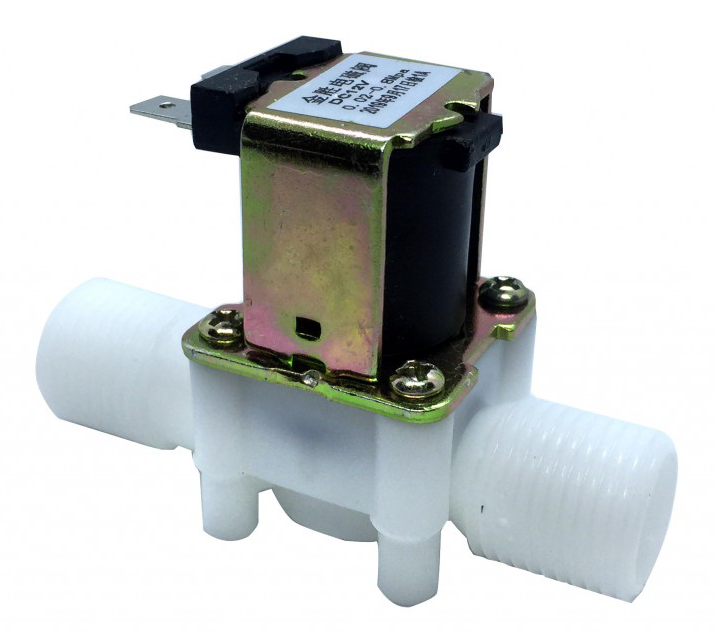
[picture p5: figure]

## Plastic Water Flow Sensor

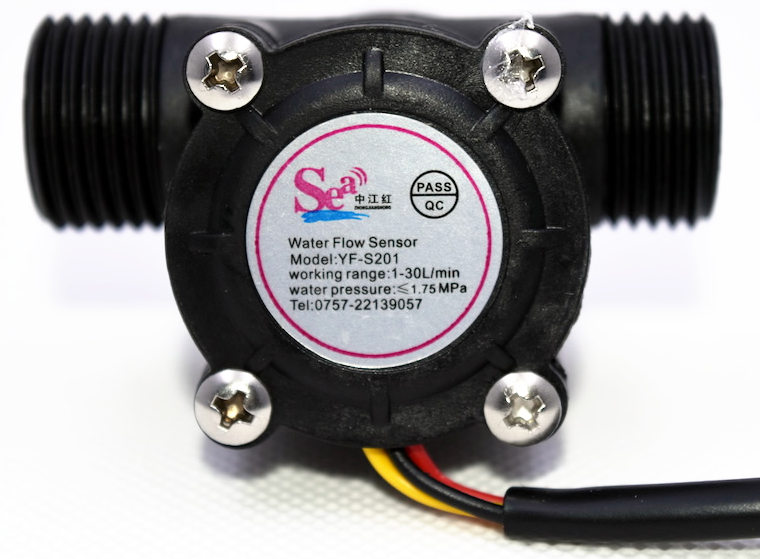
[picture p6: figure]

Features:
- ½ inch diameter PVC pipe
- 5V - 12V powered
- 13.1 (L/min) output readings
- Price: Php. 247

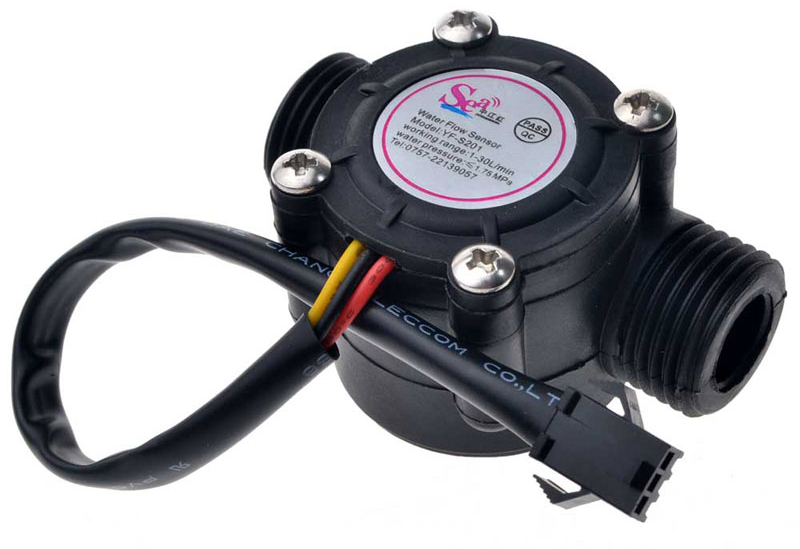
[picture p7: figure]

## Ultrasonic Ranging Sensor

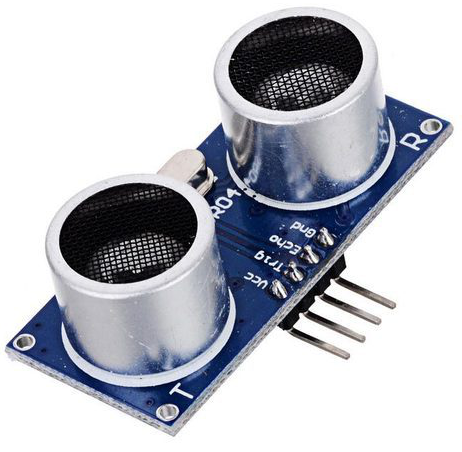
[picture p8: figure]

Features:
- ½ inch diameter PVC pipe
- 5VDC powered
- Effective angle for computation: < 30 degrees
- Ideal distance: 2cm to 500 cm
- Ultrasonic Frequency: 40k Hz
- Price: Php. 60

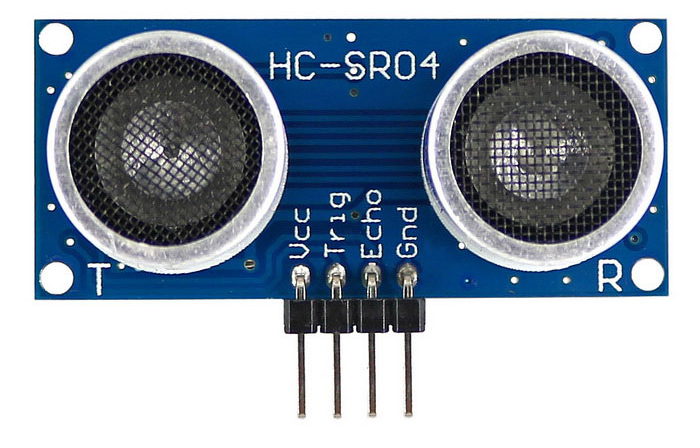
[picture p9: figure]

## Relay Module

Features:
- Power output: 250V AC 10Amps/ 125V DC 10 AMps
- 5V DC low level trigger
- 16-channel relay variation
- Price: Php. 155 (4-channel)

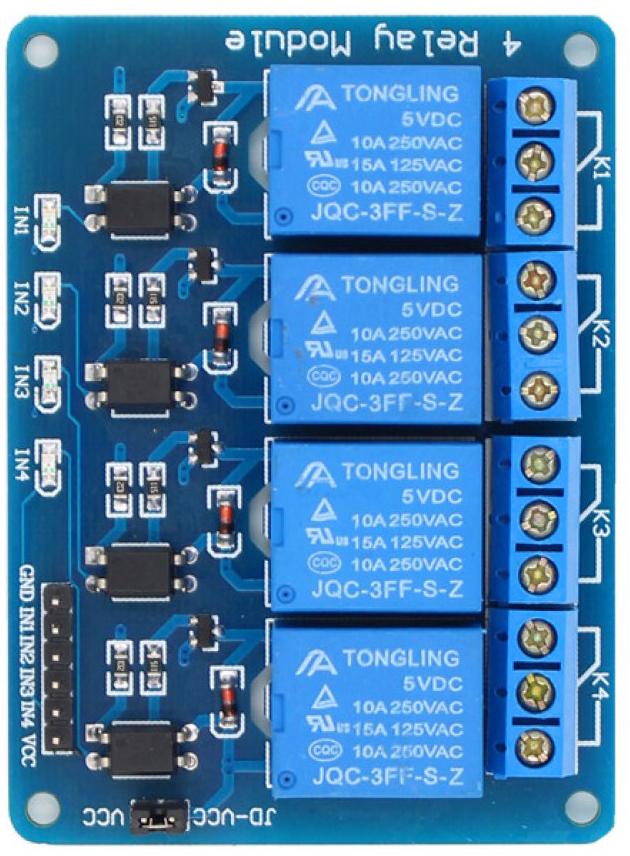
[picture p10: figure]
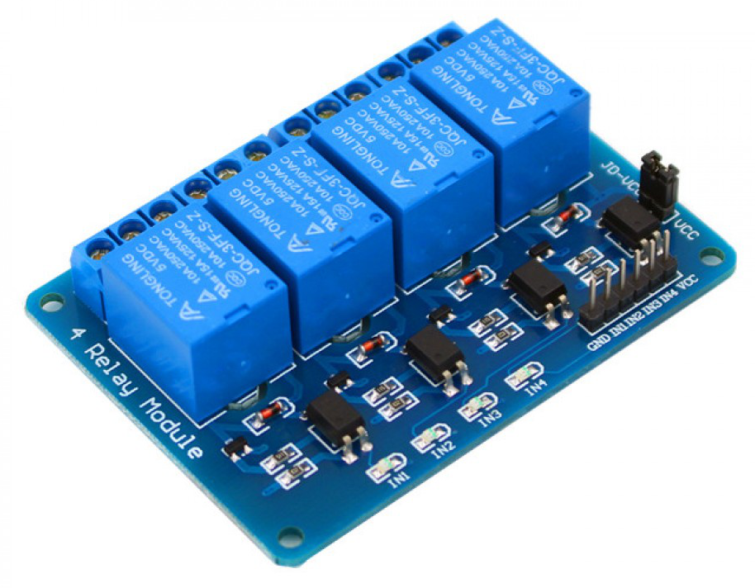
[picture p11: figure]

## MicroSD Card Reader Module

Features:
- Supports Micro SD cards, Micro SDHC card (high speed card)
- Price: Php. 79

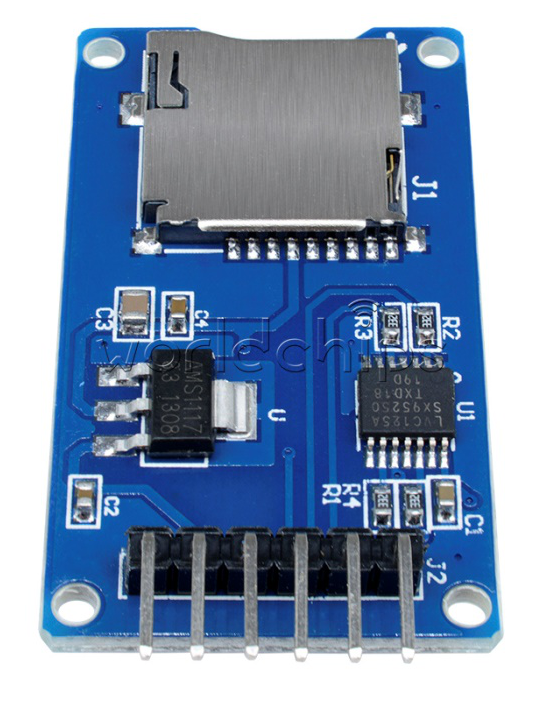
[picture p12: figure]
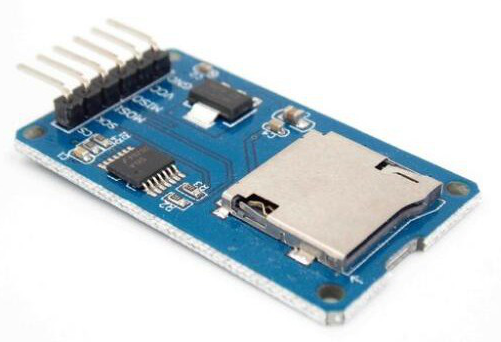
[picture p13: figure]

## NodeMCU V3 ESP8266 ESP-12E

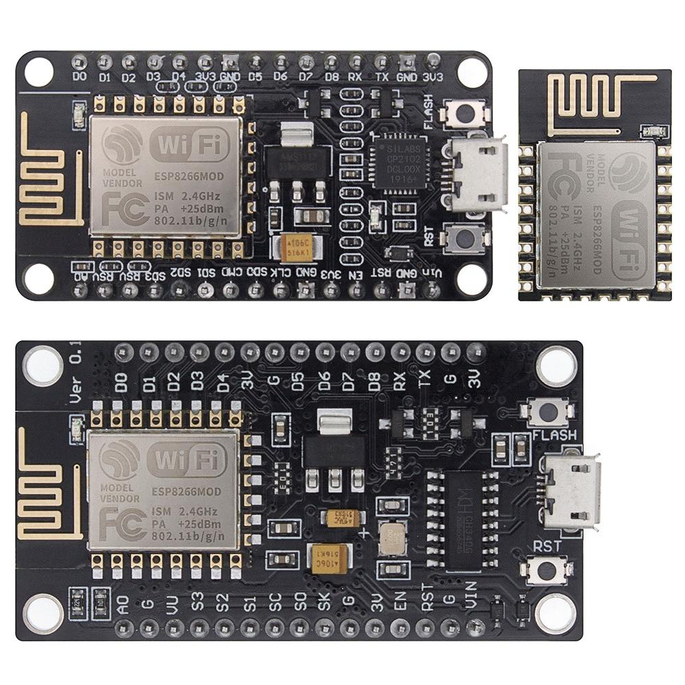
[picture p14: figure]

Features:
- Communication interface voltage: 3.3V.
- Antenna type: Built-in PCB antenna is available.
- Wireless 802.11 b/g/n standard
- WiFi at 2.4GHz, support WPA / WPA2 security mode
- Power input: 3V
- Range: ~250 meters
- Price: Php 160

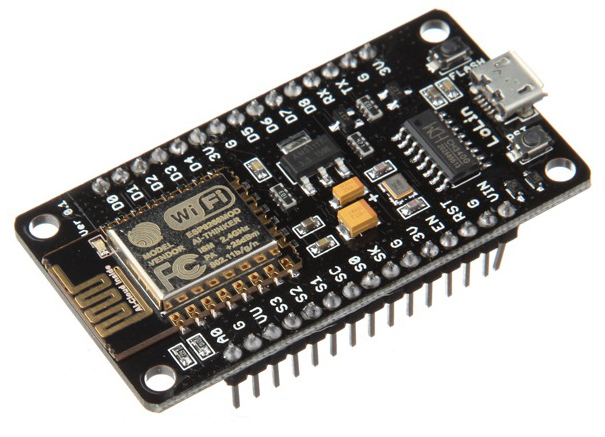
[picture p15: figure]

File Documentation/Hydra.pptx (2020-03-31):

## Hydra: Automated Plant Watering System

An Internet-of-Things Automated Plant Watering System based from Arduino and C#

Argumido | Bohol | Depanzo
BSCS 2

## Introduction

- Most people are too lazy to water their gardens or potted plants every day. Whenever we go out of town for few days, we always used to worry about our plants as they need water on regular basis. This could result to catastrophic outcomes to the plants.
- The researchers came up with a solution to automate the watering process so that gardeners, hobbyists, plant collectors – or the user him/herself would not to worry about watering or getting up early in bed to just to water his/her plants. This could lessen the effort and time of the user to maintain and water the plants.
- A system will be developed and implanted that will automatically manages and controls the watering process. The system includes a reservoir or a tank where water is being stored when main source of water is unavailable. The user will be notified based from his/her preferences and interaction with the system.

## Methodology

The device and the application will be called “HYDRA” – a serpentine water monster in Greek and Roman mythology. The Hydra System will be written in the Arduino-C programming language that controls the onsite controller functions and C# that serves as the main interface to the Hydra System.

## Methodology

The Hydra is further subdivided into two applications, the Hydra Root and the Hydra Leaf. The Hydra Root manages and controls all valves, water distribution lines (distro lines), sensors, the main pump and the main water source in the Root Distribution Line. The Hydra Leaf manages its specific distribution branch that includes its connected sensors, valves and water drip irrigation system, its built-in devices and the battery that will power the Leaf device.

## Methodology

Hydra consist of two main functions, the Water Reservoir Filling Process and the Water Distribution Process. The Water Reservoir Filling Process manages and checks the filling of the water storage tank while the Water Distribution Process manages and controls the distribution of water to the specific distribution line.

## The Hydra Onsite Setup

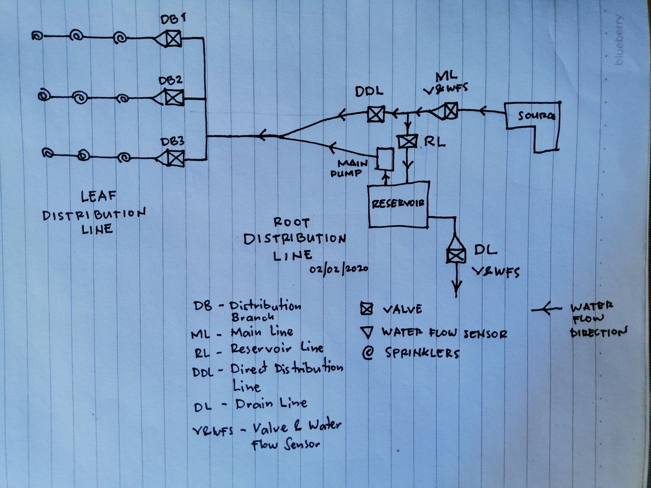
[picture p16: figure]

## Water Reservoir Filling Process

The Water Reservoir Filling Process includes 3 sub-processes:

## Filling Status

Filling status means the current water reservoir filling status of the tank which further subdivided into:
  - Empty. The tank is empty or near-to empty.
  - Filling. Water is currently filling into the tank.
  - Discharging. Water is currently distributed to the distro lines.

## Water Level

Water Level. This tells the current water level present in the tank. This includes:
  - Max Full. The maximum water level the tank could store water which value is set predefined at 95%.
  - Critical. The maximum lowest level of the water present in the tank which is set predefined at 20%.
  - Empty. The water tank is currently having no water set to the constant value of 0%.

## Water Level

Water Level. This tells the current water level present in the tank. This includes:
  - Max Full. The maximum water level the tank could store water which value is set predefined at 95%.
  - Critical. The maximum lowest level of the water present in the tank which is set predefined at 20%.
  - Empty. The water tank is currently having no water set to the constant value of 0%.

## Routines

Are methods, modes or protocols in which how the system will handle the water tank filling. Routines are classified into two:
Normal and Irregular Routines

## Normal routines

These routines are first executed by the system based from the preferences set by the user. This is further sub divided into three sub routines:

## Normal routines

Simultaneous Water Discharge-Refill routine. The water discharge and refill are done simultaneously.
Refill After Water Discharge routine. Discharges water first then refills the reservoir.
Refill then Discharge routine (Second Priority). Refills the reservoir first before water discharge. This requires an n time before a scheduled water discharge.

## Irregular Routine

These routines are executed by the system only when the system detects irregularities in the water discharge-refill process which normally occurs when the main water source is currently unavailable.

## Always open Main-to-Reservoir Line

By default, the water valve is a NC-type (Normally Closed) which means when there is no electricity feed to the valve the valve is normally closed. In this routine, the Main Line and the Reservoir Line is open for easy refilling of the tank when water from the main source is now available but closes when the tank reaches its full capacity.

## The Water Distribution Process

The water distribution process is being activated when the system reaches a certain value called the trigger.

## Normal routines

- Time. The water distribution is activated when it reaches a time first set by the user.
- Soil Moisture. The water distribution is activated when it reaches the trigger level of the soil moisture sensor first set by the user.
- Manual. A manual water distribution is carried out by the user him/herself.

## The Hydra Setup (Onsite)

## ROOT CONTROLLER (HYDRA ROOT NODE)

The Hydra Root Node controls and manages the overall function the system. It controls the:
- [1] Main Pump
- [2] Reservoir
- [3] Main Line
- [4] Distribution Line
- [5] Drain Line
- [6] Hydra Nodes (Hydra Leaf Nodes)
- [7] Main WiFi Controller (MWS)
- [8] Data Logging Service (DLS)
- [9] Notification Service (NotifS)
- [10] Leaf Node Hibernate Sequence Service (LNHSS)

## LEAF CONTROLLER (HYDRA LEAF NODE)

The Hydra Leaf Node controls and manages a specific distribution line. It controls its specific:
- [1] Distribution Valve
- [2] Distribution Water Flow Sensor
- [3] Child Soil Moisture Sensor
- [4] On-module WiFi Controller (OMWS)
- [5] On-module Data Logging Service (ODLS)
- [6] On-module Notification Service (NotifS)
- [7] On-module Hibernate Sequence (OMHS)

## The Hydra Onsite Setup

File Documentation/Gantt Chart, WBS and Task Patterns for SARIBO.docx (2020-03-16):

S.A.R.I.B.O.

(Systematic and Automated Regulation of Irrigation systems for

Backyard farming Operations)

An Arduino-based Internet-of-Things Irrigation System designed for Backyard Farming

Submitted to:

JEFFREY C. NIEDO

ITE-6 Instructor

Submitted by:

Rica S. Bohol

Jemaima D. Depanzo

Roy Joseph B. Argumido

March 3, 2020

Gantt Chart

Activities | Weeks
| 1 | 2 | 3 | 4 | 5 | 6 | 7 | 8 | 9 | 10 | 11 | 12 | 13 | 14 | 15
Planning
Analysis
Design
Development
Testing

Work Break Down Structure

Task No. | Description | Duration (Days) | Predecessor Task
1 | Prepare project titles | 3
2 | Initial project title approval | 1 | Task 1
3 | Choosing final project title | 2 | Task 2
4 | Final Project title approval | 1 | Task 3
5 | System analysis and design | 7 | Task 4
6 | Material listing, canvassing and acquisition | 9 | Task 5
7 | Programming | 56
8 | Creating and Revising individual prototype systems | 56 | Task 6, Task 7
9 | Creating the physical prototype | 21 | Task 8
10 | Initial Prototype Build and Testing | 7 | Task 8, Task 9
11 | Prepare questionnaires for initial interview and ocular inspection. | 2 | Task 10
12 | Initial Beta Testing in the site | 14 | Task 11
13 | Revision of the Prototype | 14 | Task 12
14 | Final Consultation | 1 | Task 13
15 | Final System Design | 4 | Task 14
16 | Final System Defense | 1 | Task 15
Total: | | 105 Days

Choosing Final Project Title
Start: Day 5 | ID: 3
Finish: Day 6 | Dur: 2

Task Patterns:

Prepare Project Titles
Start: Day 1 | ID: 1
Finish: Day 3 | Dur: 3

Initial Project Title Approval
Start: Day 4 | ID: 2
Finish: Day 4 | Dur: 1

Final Project Title Approval
Start: Day 7 | ID: 4
Finish: Day 7 | Dur: 1

System Analysis and Design
Start: Day 8 | ID: 5
Finish: Day 14 | Dur: 7

Material listing, canvassing and acquisition
Start: Day 15 | ID: 6
Finish: Day 23 | Dur: 9

Programming
Start: Day 24 | ID: 7
Finish: Day 80 | Dur: 56

Creating and Revising Individual Prototype Systems
Start: Day 24 | ID: 8
Finish: Day 80 | Dur: 56

Creating Physical Prototype
Start: Day 58 | ID: 9
Finish: Day 80 | Dur: 21

Final Consultation
Start: Day 95 | ID: 14
Finish: Day 95 | Dur: 1

Initial Prototype Build and Testing
Start: Day 72 | ID: 74
Finish: Day 80 | Dur: 3

Final System Design and Testing
Start: Day 96 | ID: 15
Finish: Day 100 | Dur: 4

Initial Beta Testing
Start: Day 81 | ID: 12
Finish: Day 94 | Dur: 14

Final System Defense
Start: Day 101 | ID: 16
Finish: Day 101 | Dur: 1

Revision of the Prototype
Start: Day 81 | ID: 13
Finish: Day 94 | Dur: 14

Prepare questionnaires for interview and initial ocular inspection
Start: Day 77 | ID: 11
Finish: Day 80 | Dur: 2

ISO 9001:2015 Certified Republic of the Philippines Northwest Samar State University Website: http//www.nwssu.edu.ph

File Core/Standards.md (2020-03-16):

Data Request Standards v. 2.0 rev Mar. 16, 2020
-----------------------------------------------------------
The following are the SARIBO standards used in parsing and deserializing a request table.

Request Standards Table (2 character format)
-----------------------------------------------------------
| Code  | Description |
| --- | --- |
| 10 | Distribution Line - General Request |
| 11 | Open Distribution Line |
| 20 | Soil Moisture Reading |
| 30 | Water Flow Reading |
| 40 | Power Reading |
| 50 | Time Reading |
| 51 | Perform Date and Time Sync between Leaf and Root |
| 60 | Network Reading |
| 61 | Ping Request |
| 70 | Settings |
| 71 | Synchronize Settings in the network |
| 80 | SARIBO General Channel |
| 90 | Log, High Verbosity |

Data Table
-----------------------------------------------------------
o		//Origin or where the data come from
r		//Request see Request Table
v		//Validation or return value e.g. soil moisture value

Hardware ID naming and registration:
-----------------------------------------------------------
Format: MN

Where:

M = Module type:

R = Root module
L = Leaf module

N = module number

E.g.:

L1 means Leaf Module 1

Data Process Table
-----------------------------------------------------------
Process: Leaf01 to Root Open Distribution Line
Returns:

o:	L1
r:	11
v:	887

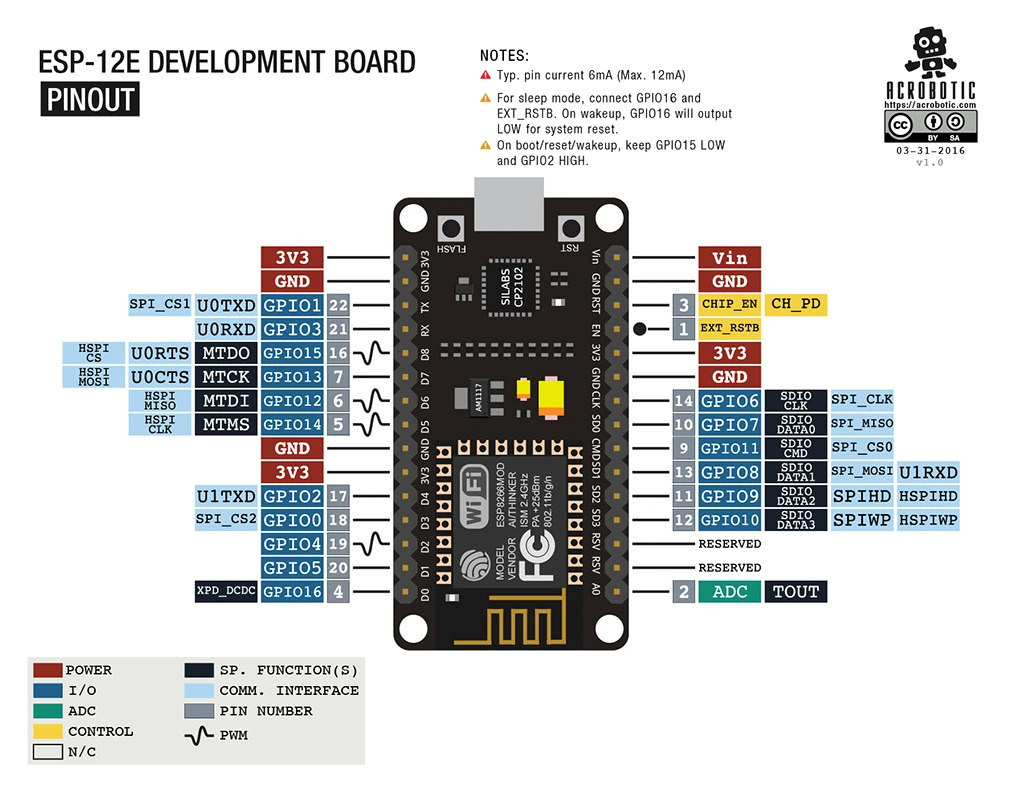
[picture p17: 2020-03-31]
Resources/NodeMCU v3 Pinout.png

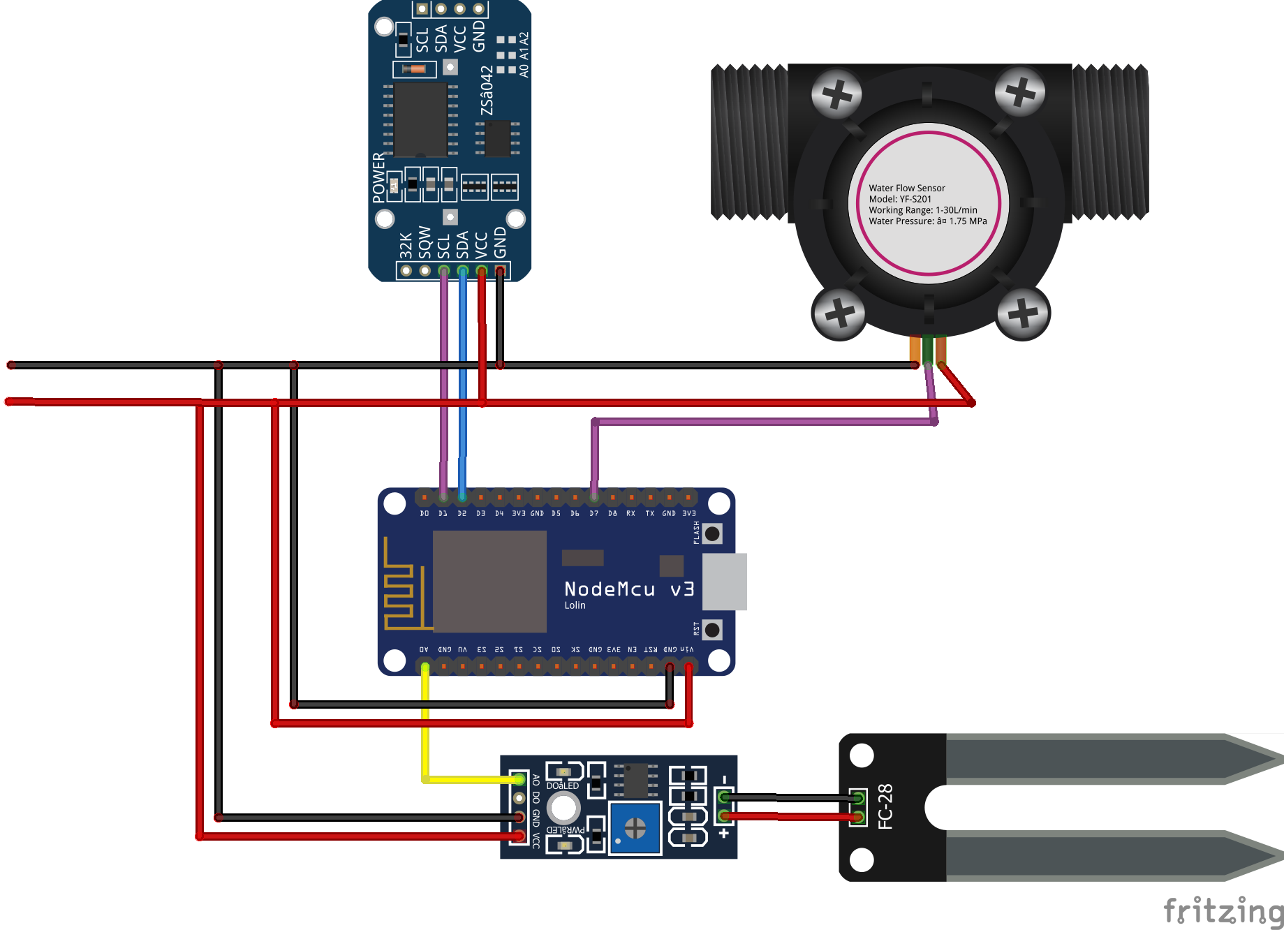
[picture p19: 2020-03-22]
Fritzing/Leaf Diagram.png

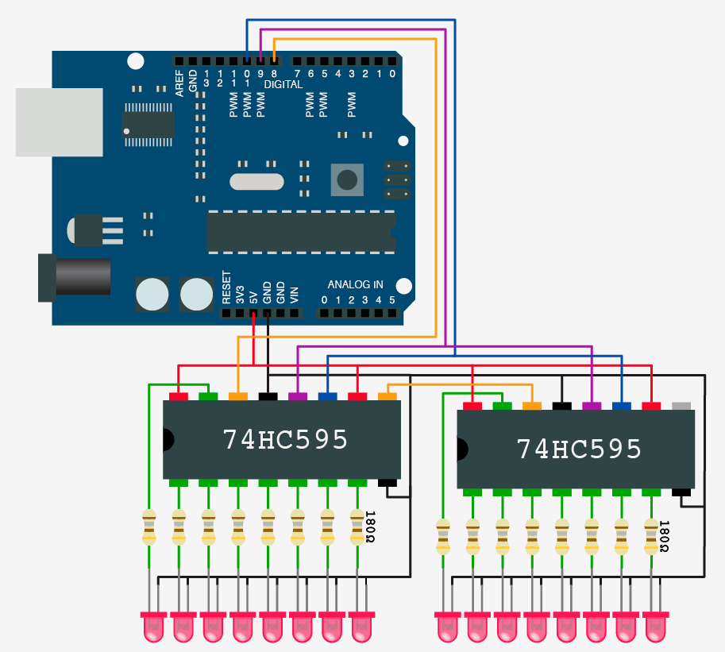
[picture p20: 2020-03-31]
Resources/74HC595 Shift Out Register 2 Daisy Chain.png

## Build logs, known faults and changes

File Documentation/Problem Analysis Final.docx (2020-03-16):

S.A.R.I.B.O.

(Systematic and Automated Regulation of Irrigation systems for

Backyard farming Operations)

An Arduino-based Internet-of-Things Irrigation System designed for Backyard Farming

Submitted to:

JEFFREY C. NIEDO

ITE-6 Instructor

Submitted by:

Rica S. Bohol

Jemaima D. Depanzo

Roy Joseph B. Argumido

March 3, 2020

Background:

Nowadays, technology has grown widely. No doubt that we are actually living in the age of technology. Technology had become an important part of our life. It increases the task an individual does in a way that a certain individual can perform various task simultaneously. The continuous increased in automation also increases the flexibility regarding work times. These inventions widely affect and changes the lives of many, it takes everyone to a new level of living.

According to House Bill No. 1718 introduced by Hon. Rozzano Rufino B. Biazon, agriculture is the traditional backbone of Philippine economy and is the principal source of employment employing almost half of the total labor force. It has been considered as a major industry source of the Philippines. However, the farmers were observed to use the traditional way of farming instead of adapting new agricultural technologies which made the agribusiness farms productive and profitable, the bill states.

Furthermore, in order for the Philippines to become a progressive, industrialized nation, it should have strong and highly productive agricultural sector. Its strength and productivity, however lies on the empowerment of the majority of the farmers and the promotion of the development of the cutting-edge agriculture technologies which enables the country to become highly competitive in the international market.

This bill is in response to the strongly felt need to integrate research and development and technology generation and transfer into a single coherent and harmonious national system dedicated to the socio-economic well-being of the farmers and to the development of the nation. It aims to transform traditional peasant agriculture to modern highly productive agriculture through generation and transfer of more productive and useful technologies of farming and rural living.

A sustained expansion of the national economy requires growth in the agricultural sector. We must transform our farmers into resource of renewed national vigor and creativity in our drive for global competitiveness.

Consequently, there is an urgent need to create strategies based on science and technology for sustainable use of water. Industrialist and researchers are working to build efficient and economic automatic systems to control water usage in order to reduces much of the wastage. Irrigation is an artificial application of watering the land for agricultural production. The requirement of water to the soil depends on soil properties such as soil moisture and soil temperature. Effective irrigation can influence the entire growth process and automation in irrigation system using modern technology can be used to provide better irrigation management. In general, most of the irrigation systems are manually operated. These traditional techniques can be replaced with automated techniques of irrigation in order to use the:

Internet of Things: Usage and Application of water efficiently and effectively. Conventionally, farmers will present in their fields to do irrigation process. Nevertheless, nowadays farmers need to manage their agricultural activity along with other occupations.

Due to the various task a person needs to do in a daily basis, monitoring and watering of plants too exhausting. Whenever we go out of town for a few days, we always used to worry about our plants as they need to be watered on regular basis. It is for the reason that we all know that plants need to be watered in order for it to thrive.

The researchers came up with a solution to automate the watering process so that farmers, gardeners, hobbyists, plant collectors will not worry about watering or getting up early in bed to just to water his/her plants. This will promote backyard farming or gardening for easy monitoring and maintenance of the plot and the plants planted on it. This could lessen the effort and time of the user to maintain and water the plants.

A system will be developed and implanted that will automatically manages and controls the watering process. The system includes a reservoir or a tank where water is being stored when main source of water is unavailable. The user will be notified based from his/her preferences and interaction with the system.

Problem Analysis:

Farming has been one of the major sources of income among various towns. Wherein Philippines is considered to be an agricultural country, considering the fact that our country relays heavily in agriculture.

According to the House Bill No. 1718, It has been said that, agriculture is the traditional backbone of Philippine economy. And it is said that, it is a principal source of employment, employing almost half of the total labor force. It has been considered as a major industry source of the Philippines.

However, the farmers were observed to use the traditional way of farming instead of adapting new agricultural technologies, which made the agribusiness farms productive and profitable.

So, farmers can use the inventions of agricultural technology in order for it to maintain the growth of its crops and even in maintaining the supply of the water whenever there are weather interruptions or any other occurrence might come along.

After identifying the problems, opportunities, objectives, and constraints throughout the making of the study, a matrix has been made.

Project: | Hydra: Automated Plant Watering System | | Project Manager: | Roy Joseph B. Argumido
Created by: | Jemaima D. Depanzo | | Last Updated by: | Rica S. Bohol
Date Created: | February 26, 2020 | | Date Last Updated: | March 3, 2020
CAUSE-AND-EFFECT ANALYSIS | | | SYSTEM IMPROVEMENT OBJECTIVES
Problem or Opportunity | | Causes and Effects | System Objectives | | System Constraints
Fetching water from the source requires too much effort. | | Farmers well be exhausted, and it would cause them to work lesser than the average due to the fact that they were already tired from fetching water to the field. | Eliminate or reduce the throughput or the amount of work being performed in fetching water. | | The availability of the water source in terms of the distance of the water source to the site.
Storing and refilling of water to the water tank requires too much effort. | | Farmers will extend too much effort in refilling their tank and storing water which may lead them to some type of illnesses and as a result they couldn't take good care of their plants. | Eliminate or reduce the throughput or the amount of work being performed in storing water. | | The availability of the water source in terms of weather conditions especially during dry seasons.
Watering the plants requires too much effort. | | Farmers will be tired in a way that they need to water the plants one by one each day and they may not be able to do other things aside from focusing on the plants. | Eliminate or reduce the throughput or the amount of work being performed in watering the plants. | | The amount of work needed in watering the plants are considerably higher.
Farmers, gardeners, plant hobbyists or people that had a backyard farm or garden needs to constantly go to the site to check for the dryness of the soil. | | Farmers cannot do any other thing aside from taking care of their plants, wherein as a person we all have different obligations or task to do aside from focusing on plants. | Eliminate or reduce the throughput or the amount of work being performed in measuring or detecting the dryness of the soil. | | Failure to detect the accurate dryness of the soil when watering the plants.

Update User

Add user

Notification

Data Logger

Time Management

Relay

Water flow Rate

Network Reading

Data Logger

Network

Time Management

Power Management

Water flow Rate

Soil Moisture Checking

fill

efill

Tank Refill

Drain

Overflow

Tank Refill

fill

efill

Tank Refill

Distribution Discharge

Hydra: Automated Plant Watering System

Root Management

Leaf Management

Tank Management

Account Management

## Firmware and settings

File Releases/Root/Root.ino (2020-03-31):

/*
  The S.A.R.I.B.O. Root Module - NodeMCU 12E esp8266 Code
  Systematic and Automated Regulation of Irrigation systems for Backyard farming Operations
  
  Stable Root (NodeMCU v3 (LoLin)) Module Code
  Version 1.3.2 Revision March 28, 2020
  
  BSD 3-Clause License
  Copyright (c) 2020, Roy Joseph Argumido (rjargumido@outlook.com)
  All rights reserved.
  
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
  1. Redistributions of source code must retain the above copyright notice, this
     list of conditions and the following disclaimer.
  
  2. Redistributions in binary form must reproduce the above copyright notice,
     this list of conditions and the following disclaimer in the documentation
     and/or other materials provided with the distribution.
  
  3. Neither the name of the copyright holder nor the names of its
     contributors may be used to endorse or promote products derived from
     this software without specific prior written permission.
  
  THIS SOFTWARE IS PROVIDED BY THE COPYRIGHT HOLDERS AND CONTRIBUTORS "AS IS"
  AND ANY EXPRESS OR IMPLIED WARRANTIES, INCLUDING, BUT NOT LIMITED TO, THE
  IMPLIED WARRANTIES OF MERCHANTABILITY AND FITNESS FOR A PARTICULAR PURPOSE ARE
  DISCLAIMED. IN NO EVENT SHALL THE COPYRIGHT HOLDER OR CONTRIBUTORS BE LIABLE
  FOR ANY DIRECT, INDIRECT, INCIDENTAL, SPECIAL, EXEMPLARY, OR CONSEQUENTIAL
  DAMAGES (INCLUDING, BUT NOT LIMITED TO, PROCUREMENT OF SUBSTITUTE GOODS OR
  SERVICES; LOSS OF USE, DATA, OR PROFITS; OR BUSINESS INTERRUPTION) HOWEVER
  CAUSED AND ON ANY THEORY OF LIABILITY, WHETHER IN CONTRACT, STRICT LIABILITY,
  OR TORT (INCLUDING NEGLIGENCE OR OTHERWISE) ARISING IN ANY WAY OUT OF THE USE
  OF THIS SOFTWARE, EVEN IF ADVISED OF THE POSSIBILITY OF SUCH DAMAGE.
 */

#include <ESP8266WebServer.h>
#include <ArduinoJson.h>
#include <ESP8266WiFi.h>
#include <RTClib.h>
#include <HCSR04.h>

HCSR04 waterLevelSensor(4, 15); //Trigger pin (GPIO 4/D2), Echo pin (GPIO 15/ D8)
RTC_DS3231 rtc;

//================= NETWORK PARAMETERS ===============
const char* ssid = "SARIBO Server - Argumido";
const char* password = "1234567890";
const char* host = "192.168.4.1";
String urlPath = "/requests/";

ESP8266WebServer server(80);
//====================================================

//========= LIST OF REGISTERED HARDWARE IDS ==========
const char* rootHID = "HF7890";
const char* leafHID[9] = {"FYF2U734", "3NIAKEK8", "B847KV34",
                              "7F3S82G3", "CF8MT6UJ", "C4I3XDO7",
                              "1J6P1520", "J56X01B5"};
//====================================================

//=============== ARDUINOJSON COMPONENTS =============
DeserializationError err;

const size_t capacity = JSON_OBJECT_SIZE(5) + 90; //For WiFi Communication
DynamicJsonDocument requestData(capacity);
DynamicJsonDocument responseData(capacity);

String requestPayload = "";
String responsePayload = "";
//====================================================

//=========== PIN CONFIGURATION TO NODEMCU ===========
int SER_Pin = 13;   //pin 14 on the 75HC595 & NodeMCU GPIO 13/D7 
int RCLK_Pin = 12;  //pin 12 on the 75HC595 & NodeMCU GPIO 12/D6
int SRCLK_Pin = 14; //pin 11 on the 75HC595 & NodeMCU GPIO 14/D5
//====================================================

//===== 74HC595 SHIFT OUT REGISTER CONFIGURATION =====
const int numberofRegisters = 2;
const int totalPins = numberofRegisters * 8;
boolean registers[totalPins];
//====================================================

//===== PIN CONFIG OF 74HC595 SHIFT OUT REGISTER =====
const int pumpPin = 0;  //Pump
const int msvPin = 1;   //Main Source Valve
const int tivPin = 2;   //Tank In Valve
const int tovPin = 3;   //Tank Out Valve
const int tdvPin = 4;    //Tank Drain Valve
//====================================================

//================ TANK CONFIGURATION ================
const float tankClearance = 3.0;  //Clearance between the sensor tip and the max full tank
float fullTankCap = 0;
float halfTankCap = 0;
//====================================================

//============== FUNCTION PROTOTYPING  ===============
void performRTCCheck();
void startServer();
void initRegisters();
String drain(const bool openDrain);
void initTank();
void writeRegisters();
void setPin(int index, int value);
void pump();
String leaf(const int leafNumber, const bool openLine);
void refillTank();
float checkWaterLevel();
String getDateTime(const int DT);
void handleRoot();
//====================================================

void performRTCCheck() {
  /* 
   *  The RTC Checking sub-program.
   *  
   *  This checks if the RTC module is connected to the Arduino and continues to loop
   *  until the RTC module is connected to the NodeMCU.
   *  
   *  Algorithm:
   *  
   *  [1] Starts the rtc module, if does not responds, loop until the rtc module is connected to NodeMCU
   *      @ if (!rtc.begin())
   *  [2] Checks if the rtc module's power is being cut or drained, then it syncs its time to Root
   *      @ if (rtc.lostPower())
   */
  if (!rtc.begin()) {
    Serial.println("Couldn't find the RTC module! Please make sure the RTC module is connected to the main board.");
    while (1);
  }

  /* 
   *  Checks if the RTC module  lost its power then synchronizes 
   *  the date and time from any connected Leaf modules
   */
  if (rtc.lostPower()) {
    Serial.println("RTC module lost power! Synchronizing time with server.");
    /*
     * The code for the date and time sncyhronization here
     * following line sets the RTC to the date & time this sketch was compiled
     */
    rtc.adjust(DateTime(F(__DATE__), F(__TIME__)));

    /* 
     *  This line sets the RTC with an explicit date & time,
     *  for example to set March 9, 2020 7:58:32 AM you would call:
     *  
     *  rtc.adjust(DateTime(year, month, day, hour, minute, second));
     *  
     *  example:
     *  rtc.adjust(DateTime(2020, 3, 8, 3, 0, 0));
     */
  }
}

void startServer() {
  Serial.println();

  Serial.println("Starting Root Module Server...");
  WiFi.softAP(ssid, password);
  IPAddress myIP = WiFi.softAPIP();

  Serial.print("SSID: ");
  Serial.println(ssid);
  Serial.print("IP Address: ");
  Serial.println(myIP);

  server.on(urlPath, handleRoot);
  server.begin();
  Serial.print("SARIBO Root Server @ ");
  Serial.print(myIP);
  Serial.println(urlPath);
  Serial.println("SARIBO Root Server running.");
}

void initRegisters() {
  pinMode(SER_Pin, OUTPUT);
  pinMode(RCLK_Pin, OUTPUT);
  pinMode(SRCLK_Pin, OUTPUT);
  
  //This clears the registers
  for(int i = totalPins - 1; i >=  0; i--){
     registers[i] = HIGH;
  }
  writeRegisters();
}

String drain(const bool openDrain) {
  String message = "";
  
  switch(openDrain) {
    case true: //OPEN DRAIN VALVE
      setPin(tdvPin, LOW);
      message = "Drain valve open.";
      break;

    case false: //CLOSE DRAIN VALVE
      setPin(tdvPin, HIGH); //Closes the Drain Valve
      message = "Drain valve closed.";
      break;

    default:
      message = "Unable to perform open/close drain valve.Invalid open drain valve command.";
      break;
  }
  return message;
}

void initTank() {
  double currTCap = 0.0;
  double totalTReads = 0.0;
  int i;

  drain(true);  //Opens the drain valve to ensure tank is empty during initialization
  
  for(i = 1; i < 11; i++) {
    currTCap = waterLevelSensor.dist();
    totalTReads += currTCap;
    Serial.print("Reading #");
    Serial.print(i);
    Serial.print(": ");
    Serial.print("Current: ");
    Serial.println(currTCap);
    delay(1000);
  }

  if(i == 11) {
    fullTankCap = (totalTReads / 10) - tankClearance;
    halfTankCap = fullTankCap / 2;
    Serial.print("Full Tank: ");
    Serial.println(fullTankCap);
  }
  Serial.println("Tank refill on process.");
}

void writeRegisters() {
  digitalWrite(RCLK_Pin, LOW);

  for(int i = totalPins - 1; i >=  0; i--){
    digitalWrite(SRCLK_Pin, LOW);

    int val = registers[i];

    digitalWrite(SER_Pin, val);
    digitalWrite(SRCLK_Pin, HIGH);
  }
  digitalWrite(RCLK_Pin, HIGH);
}

void setPin(int index, int value) {
  /*
   * Set an individual pin HIGH or LOW
   */
  registers[index] = value;
  writeRegisters();
}

void pump() {
  int countOpenLeafLines = 0;
  for(int i = 8; i < totalPins; i++){
     if(registers[i] == 0)  // Leaf Distribution Line is OPEN
      countOpenLeafLines++;
  }
  
  if(countOpenLeafLines == 0) //There is no more open distribution lines
    setPin(pumpPin, HIGH);  //PUMP OFF
  else
    setPin(pumpPin, LOW);  //PUMP ON
}

String leaf(const String hID, const bool openLine) {
  String message = "";
  int leafPin = 0;

  for(int i = 0; i < 8; i++) {
    if((String)leafHID[i] == hID) {
      leafPin = i + 8;
    }
  }
  /*
   * Checks if the leaf to be open has a registered pin number in the system
   * based on the total number of pins available.
   */
  if(leafPin < totalPins) {
    switch(openLine) {
      case true:  //opens the specific leaf distribution line
        setPin(leafPin, LOW);
        message =  "Leaf " + (String)(leafPin-7) + " distribution line opened.";
        break;

      case false:  //opens the specific leaf distribution line
        setPin(leafPin, HIGH);
        message = "Leaf " + (String)(leafPin-7) + " distribution line closed.";
        break;
    }
  } else {
    if(openLine == true)
      message = "Unable to open Leaf " + (String)(leafPin-7) + " distribution line.";
    else
      message = "Unable to close Leaf " + (String)(leafPin-7) + " distribution line.";
  }
  pump();
  return message;
}

void refillTank() {
  const int waterLevel = checkWaterLevel();
  
  Serial.print("Current Tank Capacity: ");
  Serial.print(waterLevel);
  Serial.print("%");
  Serial.print("\tFull Capacity: ");
  Serial.println(fullTankCap);
  
  if(waterLevel > 101) {
    /*
     * AUTOMATIC WATER TANK SPILL TRIGGER
     * 
     * The current tank water level exceeds the maximum tank capacity set by the system,
     * this will drain the tank for 5 seconds then closes after the time. This is to avoid
     * water to distroy the ultrasonic ranging sensor.
     */
    Serial.println("Current water level exceed maximum tank capacity! Spilling excess water.");
    setPin(pumpPin, HIGH);  //Pump Off
    setPin(msvPin, HIGH);  //Main Source Valve Off
    setPin(tivPin, HIGH);  //Tank In Valve Off
    setPin(tovPin, HIGH);  //Tank Out Valve Off
    drain(true);
    delay(5000);
    drain(false);
  } else if(waterLevel < 50) {
    /*
     * WATER TANK REFILL PROCESS
     * 
     * The current water level in the tank is lesser than the half capacity of the tank.
     * This will pauses all watering process to prioritizes the refill of the tank
     * to ensure that the tank has a sufficient amount of stored water for the system and
     * resumes all watering process when the tank is full.
     */
    
    Serial.println("Water tank refill on process.");
    drain(false); //Closes the drain valve
    setPin(pumpPin, LOW);  //Pump On
    setPin(msvPin, LOW);  //Main Source Valve On
    setPin(tivPin, LOW);  //Tank In Valve On
    setPin(tovPin, HIGH);  //Tank Out Valve Off
    
    while(checkWaterLevel() < 101) {
      Serial.println("Refilling...");
      delay(1000);
    }
    
    setPin(pumpPin, HIGH);  //Pump Off
    setPin(msvPin, HIGH);  //Main Source Valve Off
    setPin(tivPin, HIGH);  //Tank In Valve Off
    
  } else if(waterLevel > 50 && waterLevel < 101){
    /* 
     *  TANK IN SUFFICIENT WATER LEVEL
     */
    Serial.println("Sufficient tank water level.");
    drain(false); //Closes the drain valve
    setPin(msvPin, HIGH);  //Main Source Valve Off
    setPin(tivPin, HIGH);  //Tank In Valve Off
  }
}

float checkWaterLevel() {
  float currTankCap = ((ceil(fullTankCap - (waterLevelSensor.dist() - tankClearance))) / fullTankCap) * 100;
  return currTankCap;
}

String getDateTime(const int DT) {
  /* 
   *  The get Date and Time sub-program.
   *  
   *  This returns the current date and time set in the RTC module.
   *  This requires a constant integer parameter to return the
   *  neccessary DateTime string based on the asked value, based
   *  on the following parameter values:
   *  
   *  0 = returns the current date as a String
   *  1 = returns the current time as a String
   *  2 = return the current date and time with a newline delimiter as a String
   *  
   *  Algorithm:
   *  
   *  [1] Converts default the 24-hour format to 12-hour format with AM/PM designation
   *      @ if(now.hour() > 12) 13:24:35 -> 1:24:35 PM
   *  [2] Adds the '0' padding to the minute and second if the value is less than 10
   *      e.g. 8:7:9 -> 8:07:09
   *      @ if(now.minute() < 10) & if(now.second() < 10)
   *  [3] Creates the String Date and Time.
   *      @ String Date = ...; and String Time = ...;
   *  [4] Returns the Date or Time request or the error message as String
   */
  String HF = ""; // AM/PM time notation
  int h = 0;  //holder for the current hour value
  String m = "";
  String s = "";
  const char monthNames[12][12] = {"January", "February", "March",
                                   "April", "May", "June", "July",
                                   "August", "September", "October",
                                   "November", "December"};

  DateTime now = rtc.now();

  // Converting 24H to 12H with AM/PM designation
  if(now.hour() > 12) {
    h = now.hour() % 12;
    HF = " PM";
  }else
  {
    h = now.hour();
    HF = " AM";
  }

  // Adding the '0' Padding to minute if minute is lesser than 10
  if(now.minute() < 10) { m = "0" + (String)now.minute(); }
  else { m = (String)now.minute(); }

  // Adding the '0' Padding to second if second is lesser than 10
  if(now.second() < 10) { s = "0" + (String)now.second(); }
  else { s = (String)now.second(); }

  String Date =  (String)monthNames[now.month()] + ' ' + (String)now.day() + ", " + (String)now.year();
  String Time = (String)h + ':' + (String)m + ':' + (String)s + (String)HF;

  switch(DT)
  {
    case 0:
      return Date;
      break;

    case 1:
      return Time;
      break;

    case 2:
      return (String)Date + '\n' + (String)Time;
      break;

    default:
      return "Invalid getDateTime return code! \n0 = returns the current date\n1 = returns the current time\n2 = returns the current date and time.";
      break;
  }
}

void handleRoot() {
  if (server.hasArg("data")) {
    requestPayload = server.arg(0);
    Serial.println("Leaf request data recieved.");
  }

  err = deserializeJson(requestData, requestPayload);
  if (err) {
      Serial.print(F("Unable to decode message! Error: "));
      Serial.println(err.c_str());
  }

  const char* origin = requestData["origin"];
  const char* datesent = requestData["datesent"];
  const char* timesent = requestData["timesent"];
  int request = requestData["request"];
  int value = requestData["value"];

  String resp = "";
  switch(request) {
    case 11:  //open distribution line request
      resp = leaf(origin, true);
      break;

    case 12:  //open distribution line request
      resp = leaf(origin, false);
      break;
  }

  Serial.println("============ REQUEST INFORMATION ============");
  Serial.print("Origin: ");
  Serial.println(origin);

  Serial.print("Date Sent: ");
  Serial.println(datesent);

  Serial.print("Time Sent: ");
  Serial.println(timesent);

  Serial.print("Request: ");
  Serial.println(request);

  Serial.print("Value: ");
  Serial.println(value);
  Serial.println("=============================================");

  responseData["origin"] = "HF7890";
  responseData["datesent"] = getDateTime(0);
  responseData["timesent"] = getDateTime(1);
  responseData["request"] = 10;
  responseData["value"] = resp;

  responsePayload = "";
  serializeJson(responseData, responsePayload);

  server.send(200, "text/plain", responsePayload);
}

void setup() {
  Serial.begin(115200);
  initRegisters();
  //initTank();
  //performRTCCheck();
  //startServer();
}

void loop() {
	//server.handleClient();
	Serial.println(leaf("FYF2U734", true));
	delay(5000); 

	Serial.println();
	delay(5000); 
}

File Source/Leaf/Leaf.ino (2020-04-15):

/*
  The S.A.R.I.B.O. Leaf Module - NodeMCU-12E v3 esp8266 Module Code
  Version 1.3.1 Revision April 16, 2020
  Systematic and Automated Regulation of Irrigation systems for Backyard farming Operations
  
  BSD 3-Clause License
  Copyright (c) 2020, Roy Joseph Argumido (rjargumido@outlook.com)
  All rights reserved.
  
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
  1. Redistributions of source code must retain the above copyright notice, this
     list of conditions and the following disclaimer.
  
  2. Redistributions in binary form must reproduce the above copyright notice,
     this list of conditions and the following disclaimer in the documentation
     and/or other materials provided with the distribution.
  
  3. Neither the name of the copyright holder nor the names of its
     contributors may be used to endorse or promote products derived from
     this software without specific prior written permission.
  
  THIS SOFTWARE IS PROVIDED BY THE COPYRIGHT HOLDERS AND CONTRIBUTORS "AS IS"
  AND ANY EXPRESS OR IMPLIED WARRANTIES, INCLUDING, BUT NOT LIMITED TO, THE
  IMPLIED WARRANTIES OF MERCHANTABILITY AND FITNESS FOR A PARTICULAR PURPOSE ARE
  DISCLAIMED. IN NO EVENT SHALL THE COPYRIGHT HOLDER OR CONTRIBUTORS BE LIABLE
  FOR ANY DIRECT, INDIRECT, INCIDENTAL, SPECIAL, EXEMPLARY, OR CONSEQUENTIAL
  DAMAGES (INCLUDING, BUT NOT LIMITED TO, PROCUREMENT OF SUBSTITUTE GOODS OR
  SERVICES; LOSS OF USE, DATA, OR PROFITS; OR BUSINESS INTERRUPTION) HOWEVER
  CAUSED AND ON ANY THEORY OF LIABILITY, WHETHER IN CONTRACT, STRICT LIABILITY,
  OR TORT (INCLUDING NEGLIGENCE OR OTHERWISE) ARISING IN ANY WAY OUT OF THE USE
  OF THIS SOFTWARE, EVEN IF ADVISED OF THE POSSIBILITY OF SUCH DAMAGE.
 */

#include <SD.h>
#include <SPI.h>
#include <ArduinoJson.h>
#include <ESP8266WiFi.h>

//================= PIN CONFIGURATION ================
const int sdCS = 15;
const int smVCC = 5;
const int smAP = 0;
//====================================================

//======================= CACHE ======================
const int _sleep = 5;
const int maxBuffer = 2000;
const long int sleepTime = 1000000 * _sleep;
const char* coreFN = "System/CoreConfig.txt";

File file;
IPAddress myIP;
int ngid = 0;
int sdfail = 0;
int hostfail = 0;
int loadfail = 0;
int sconnfail = 0;
int serverfail = 0;
int irrReadfail = 1;
bool startWater = false;
int reads = 0;
unsigned long bootInit;

String repDir;
String logsDir;
String root;
String local;
String ssid;
String key;
String host;
String reqpath;
int port;
int rFail = 1;
int rSoil;
int rGen;
int rOpen;
int rClose;
String wut;
int smrp;
int maxd;
int mind;
int ideal;
//====================================================

//============== ARDUINOJSON COMPONENTS ==============
const size_t desBuffer = JSON_OBJECT_SIZE(4) + maxBuffer;
const size_t fileBuffer = JSON_OBJECT_SIZE(28) + maxBuffer;
DynamicJsonDocument settingsData(fileBuffer);
DynamicJsonDocument exchangeData(desBuffer);
//====================================================

void initSD() {
  pinMode(sdCS, OUTPUT);
  while(!SD.begin(sdCS)) {
    if(sdfail == 60) {
      ESP.restart();
    } else {
      Serial.println("Unable to detect the SD Card module!");
      sdfail++;
      delay(1000);
    }
  }
}

String generateTID() {
  return local + '-' + String(++ngid);
}

String decodeJsonData(const DeserializationError error) {
  if(error)
    return "Error " + (String)error.c_str();
  else
    return "No decoding error.";
}

void loadLeafSettings() {
  char data[maxBuffer];
  int i = 0;
  
  file = SD.open(coreFN);
  while(!file) {
    loadfail++;
    Serial.println("Unable to load settings!");
    delay(1000);
    file = SD.open(coreFN);
  }

  while(file.available()) {
    data[i] = file.read();
    i++;
  }
  data[i] = '\0';

  String decodeSF = decodeJsonData(deserializeJson(settingsData, data));
  
  repDir = settingsData["repdir"].as<String>();
  logsDir = settingsData["logsdir"].as<String>();
  rSoil = settingsData["rsoil"].as<int>();
  rGen = settingsData["rgen"].as<int>();
  rOpen = settingsData["ropen"].as<int>();
  rClose = settingsData["rclose"].as<int>();
  root = settingsData["root"].as<String>();
  local = settingsData["local"].as<String>();
  ssid = settingsData["ssid"].as<String>();
  key = settingsData["key"].as<String>();
  host = settingsData["host"].as<String>();
  reqpath = settingsData["reqpath"].as<String>();
  port = settingsData["port"].as<int>();
  wut = settingsData["wut"].as<String>();
  smrp = settingsData["smrp"].as<int>();
  maxd = settingsData["maxd"].as<int>();
  mind = settingsData["mind"].as<int>();
  ideal = settingsData["ideal"].as<int>();

  Serial.println("Settings successfully loaded into the cache.");
  file.close();
}

void connectToServer() {  
  WiFi.mode(WIFI_STA);
  WiFi.begin(ssid, key);
  
  Serial.println("Connecting to " + ssid + "...");
  while(WiFi.status() != WL_CONNECTED) {
    
    serverfail++;
    delay(1000);
  }

  myIP = WiFi.localIP();
  Serial.println("Connected to Server after " + (String)serverfail + " seconds.");
  Serial.println("Leaf IP Address: " + myIP.toString());
}
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

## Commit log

2020-03-19 Test Leaf Prototype Lolin
2020-03-19 Test Root Prototype Lolin
2020-03-19 Prototype for WiFi Leaf Communication
    SARIBO PROTOTYPE FOR WIFI COMMUNICATION - LEAF MODULE
2020-03-19 Prototype for WiFi Root Communication
    SARIBO PROTOTYPE FOR WIFI COMMUNICATION - ROOT MODULE
2020-03-19 Moving to its Arduino Repository
2020-03-20 Added verbosity Serial printing for sanity check.
2020-03-20 Root WiFi Prototype Version 1.2
2020-03-20 Leaf Version 1.2.6 adding WiFi communication
    Leaf Version 1.2.6 could be used with Root WiFi Prototype Version 1.2 for testing
2020-03-20 Root Prototype Module v1.2
    Compatible to SARIBO Version 1.2.4 and higher
    Version 1.2 Revision March 20, 2020
    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
2020-03-20 Stable Leaf Module Prototype v1.2
    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
2020-03-21 Stable Leaf Wifi Communication Prototype v1.3
2020-03-21 Stable Root Wifi Communication Prototype v1.3
2020-03-21 Stable NodeMCU Root Module v1.1.3
    Added WiFi communication and Date and Time functionality with no attachment to Arduino Nano
2020-03-21 Moving to its official Arduino repository
2020-03-21 Sample Arduino Codes
2020-03-22 STABLE SARIBO ROOT MODULE PROTOTYPE v1.1.4
    With serial communication to Root NodeMCU
2020-03-22 OFFICIAL STABLE RELEASE - LEAF v1.2.7
    OFFICIAL STABLE RELEASE - Leaf Module, Arduino Nano Code Version 1.2.7 Revision March 22, 2020
2020-03-22 OFFICIAL STABLE RELEASE - Root Arduino Nano v1.2.7
    OFFICIAL STABLE RELEASE - Root Module, Arduino Nano Code Version 1.2.7 Revision March 22, 2020
2020-03-22 Fritzing Parts and Diagram
    [Leaf.fzz, Root Diagram.fzz]
2020-03-25 Shift Register Prototype System for SARIBO v1.2.7
2020-03-25 Updated pump() auto-power
    Pump will be OFF when there is NO OPEN LEAF DISTRIBUTION LINE
2020-03-27 Adopting new stable Root prototype
2020-03-27 Stable Root Module - NodeMCU v3 Code v.1.3.1
    Arduino Nano is removed, adopting only the NodeMCU as the sole processor to reduce cost and complexity to the system. Optimized leaf relay switching, refill and drain processes.
2020-03-27 Stable Root Module v.1.3.1 (NodeMCU v3 code)
    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
2020-03-27 SARIBO Generate Hardware ID Prototype Function
    Generates a random, 8-alphanumeric character String e.g. 5E6Q0716, H1YNUY0I, GRS5OS0U, etc.
2020-03-31 Settings Prototype Function v1.1 rev 1 April 2020
    Able to create, retrieve and update settings in a a file in SD Card
2020-03-31 Added pin configuration table
2020-03-31 Added sample values to Data Management Table
2020-03-31 Updating Friting Diagrams
    [Leaf.fzz, Relay Expansion Board.fzz, SARIBO.fzz]
2020-04-02 Settings Prototype Function v1.2
2020-04-03 Leaf Settings Prototype Function v1.1
2020-04-05 SARIBO Leaf April 5, 2020 Design
    [SARIBO Leaf April 5, 2020 Design.fzz]
2020-04-13 Soil Moisture Check Prototype function v1.1.3
2020-04-13 Rename Individual Systems/DMS/DMS.ino to Prototype Functions/LeafDMS/LeafDMS.ino
    Moving to its new repository
2021-11-18 Added sample Serial Communication using NodeMCU
    Serial Communication between NodedMCU (Sender) and Arduino (Receiver)
2021-11-18 Added sample Serial Communication using Arduino
    Serial Communication between NddeMCU (Sender) and Arduino (Receiver)
